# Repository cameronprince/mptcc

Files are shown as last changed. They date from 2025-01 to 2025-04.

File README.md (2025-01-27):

# MicroPython Tesla Coil Controller (MPTCC)

A MicroPython-based controller for Tesla coils, developed by Cameron Prince.

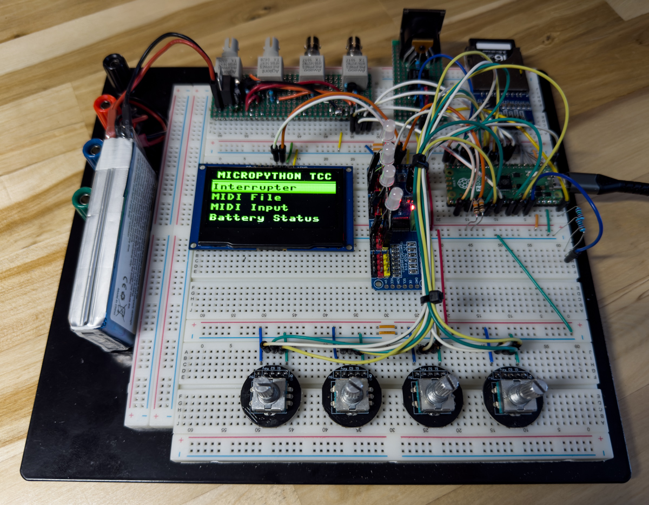
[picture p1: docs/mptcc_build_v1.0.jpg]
MicroPython Tesla coil controller build


This project is based on the MIDI Pro Tesla Coil Controller (also MPTCC) by Phillip Slawinski. A best
effort was made to maintain control functionality matching Phillip's controller, along with feature
parity with the initial Interrupter, MIDI File and MIDI Input screens. A few new features were added
as well, and more are planned.

The controller has four outputs which can drive fiber optic transmitters of your choice, or you may
use other connectors, such as BNC, with shielded cables. The controller sends pulsed square waves of
a frequency and duty cycle you control with the rotary encoders while on the Interrupter screen. On the MIDI
input screen, the controller takes the notes it receives from a MIDI instrument and converts them into
pulses matching the frequency and velocity of the received notes and sends them to all outputs.

The MIDI File screen lists MIDI files found on the SD card and allows you to map tracks within a selected
file with each of the four outputs. During playback, the four rotary encoders control the levels of
each output. The RGB LEDs are active any time the outputs are active and their colors match the relative
level of each output with colors ranging from green, to yellow, to red.

This software provides a framework for any number of screens with each screen optionally having any number
of sub-screens. The rotary encoder and pushbutton inputs cascade down to each screen or sub-screen,
ensuring that all code for a particular screen is contained within its class. Adding your own screens
to customize the controller should be pretty straightforward.

Please be aware that this is my first significant work with MicroPython. I am certain this software can
be improved in many ways and I invite anyone to participate.

## Table of Contents

- [Warning](#warning)
- [Features](#features)
- [Hardware](#hardware)
- [Dependencies](#dependencies)
- [Diagram](#diagram)
- [Connections](#connections)
- [Installation](#installation)
- [Usage](#usage)
- [File Descriptions](#file-descriptions)
- [License](#license)
- [Credits](#credits)

## Warning

Tesla coils are dangerous devices which can cause shocks, burns, fires and even death. The author assumes no
responsibility for any devices operated by the controller project described herein, or for any damage or
injury that may be caused by their operation.

This controller is experimental. If not assembled and operated correctly, it can cause damage to driver and
bridge components. It is solely up to the builder to verify the controller output prior to connecting it to
a Tesla coil. The author assumes no responsibility for damage to equipment, components, tools, etc. which can be
caused by the use of this controller. You have been warned.

## Features

- Class-based, modular screen management system
- Interrupt-driven inputs/non-polling design
- Utilizes threads for driving outputs
- Standard interrupter (square wave pulse generator) with variable frequency and on time and user configurable limits (currently drives all four outputs equally)
- MIDI file playback from SD card with elapsed time display and interface for mapping tracks to outputs - rotary encoders allow level control for each output
- Automatic scrolling of long file and track names
- MIDI input (currently drives all four outputs from a single input/channel)
- RGB LEDs display relative output levels as colors ranging from green, to yellow, to red
- Battery status monitoring
- User configuration stored in flash memory with restore defaults feature
- Intuitive menu system and navigation
- Easily expandable to support additional features
- Supports SSD1306, SSD1309, SSD1322 displays
- Supports standard quadrature rotary encoders and I2CEncoders w/ RGB LED
- Tested with both Raspberry Pi Pico 2 and ESP-WROOM-32

## Hardware
1. Raspberry Pi Pico 2 (Qty 1) [Buy](https://amzn.to/4hhQxz3) - or similar MicroPython-compatible microcontroller with at least two cores
2. PCA9685 16-channel 12-bit PWM (Qty 1) [Buy](https://amzn.to/4jf2E1J)
3. SD card reader (Qty 1) [Buy](https://amzn.to/40gHUhw)
4. Rotary encoder w/ switch (Qty 4) [Buy](https://www.amazon.com/dp/B0BGR4JPRK)
5. RGB LED (Qty 4) [Buy](https://amzn.to/3PD5WhP)
6. 2.4" SSD1309 OLED display (Qty 1) [Buy](https://amzn.to/40wQWbs) - or similar I2C-driven display with MicroPython frame buffer driver
7. 5-Pin DIN socket (Qty 1) [Buy](https://amzn.to/40hERpg)
8. 2N4401 NPN transistors (Qty 4) [Buy](https://amzn.to/4aikSeu)
9. 6N138 high-speed optocoupler (Qty 1) [Buy](https://amzn.to/3BXwgA4)
10. Fiber optic transmitters or connectors of your choice for outputs (Qty 4)
11. Various 1/4-watt resistors [Buy](https://amzn.to/3DXIOYx)
12. 1N4148 diode (Qty 1) [Buy](https://amzn.to/4hi579Q)
13. 5VDC power source (Qty 1) [Buy](https://amzn.to/3Wre4pd)
14. Optional breadboard (Qty 1) [Buy](https://amzn.to/4hkUC5s)

Total estimated cost: $160 USD (not including output transmitters or connectors)

## Dependencies
- Display driver ([MicroPython-SSD1306](https://github.com/TimHanewich/MicroPython-SSD1306))
- External PWM driver ([pca9685_for_pico](https://github.com/kevinmcaleer/pca9685_for_pico))
- Rotary encoder driver ([micropython-rotary](https://github.com/miketeachman/micropython-rotary))
- SD card reader driver ([sdcard.py](https://github.com/micropython/micropython-lib/blob/master/micropython/drivers/storage/sdcard/sdcard.py))
- MIDI input decoder ([SimpleMIDIDecoder](https://github.com/diyelectromusic/sdemp/blob/main/src/SDEMP/Micropython/SimpleMIDIDecoder.py))
- MIDI file parser ([umidiparser](https://github.com/bixb922/umidiparser))

## Schematic

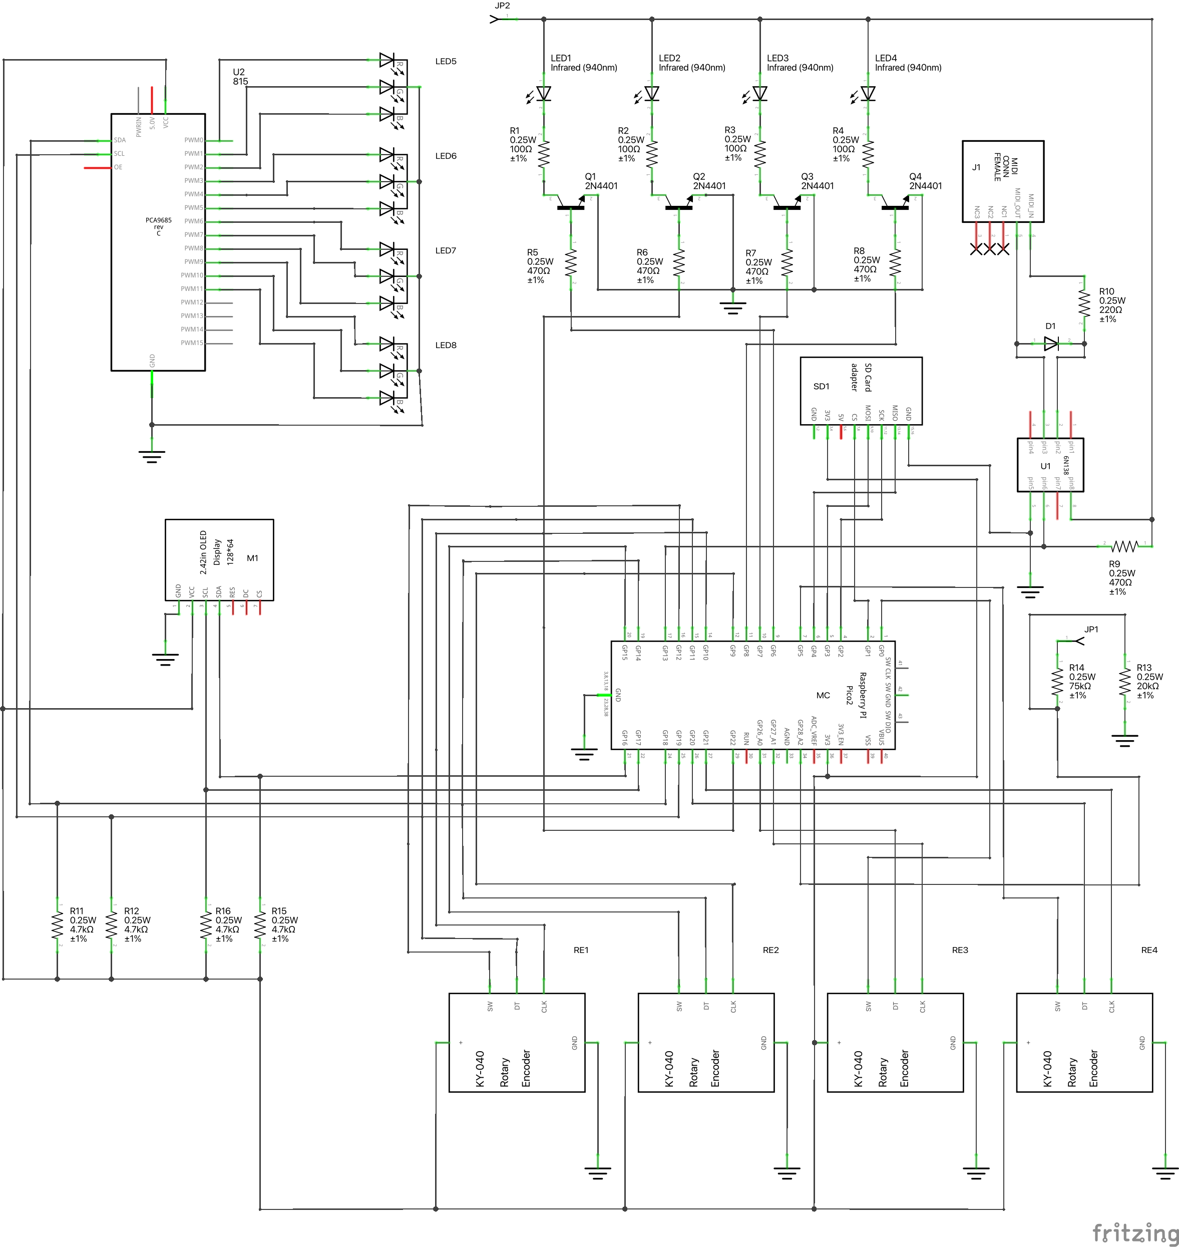
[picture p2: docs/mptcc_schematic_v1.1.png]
MicroPython Tesla coil controller schematic


## Diagram

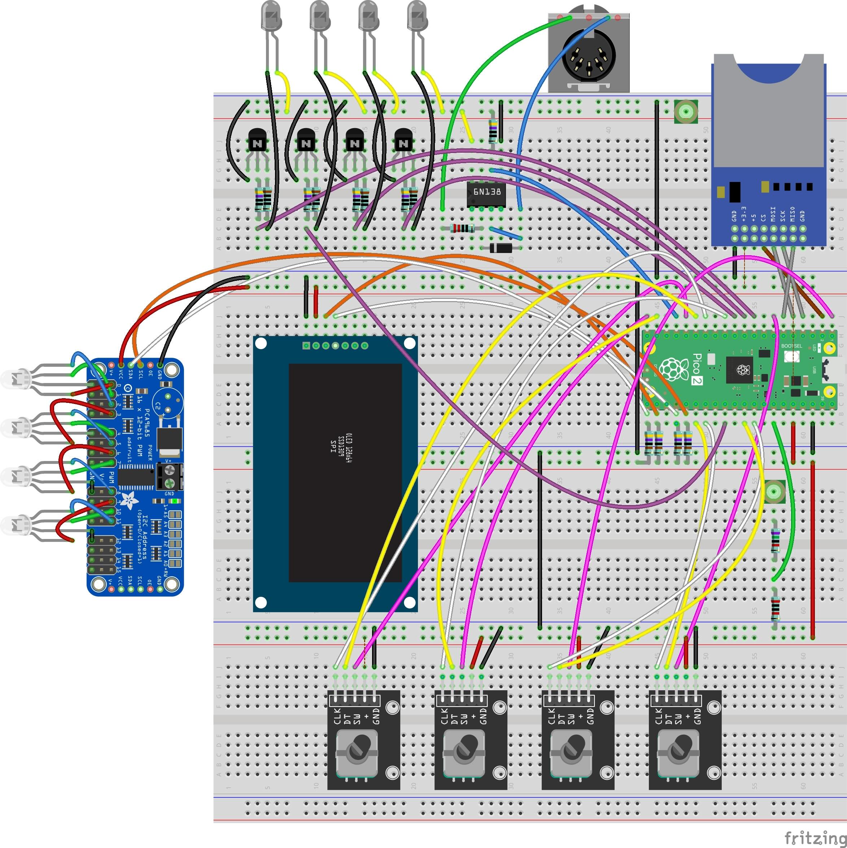
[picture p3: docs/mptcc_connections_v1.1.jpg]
MicroPython Tesla coil controller connections


You can download the Fritzing file for this project [here](docs/mptcc_v1.1.fzz).

## Installation

1. Clone the repository:

    ```bash
    git clone https://github.com/cameronprince/mptcc.git
    ```

2. Copy the project files to your MicroPython-compatible device. Typically, you place the entire mptcc directory into the root directory of your device.

3. Ensure you have the required dependencies installed on your device. The dependencies listed above should be placed into a lib subdirectory in the root directory of your device.

4. Edit the mptcc/init.py file and update any hardware variables for which your project deviates from the provided schematics and connection diagrams.

5. Run main.py

Custom firmware build instructions coming soon.

## Usage

### General Operation

Rotate encoder 1 to scroll through the main menu options. Press encoder 1 pushbutton to navigate to a sub-menu item
or select a screen. Pressing encoder 2 pushbutton is consistently used as the "back" or "return" button.

### Interrupter

On the interrupter screen, encoder 1 rotation sets output on time. Encoder 2 rotation sets
output frequency. Press encoder 3 pushbutton to enable/disable outputs. Pressing encoder 4
pushbutton triggers 10x mode where the frequency and on time increments by 10 rather than
the default of 1. To return to the main menu, press encoder 2 pushbutton.

### MIDI Input

When MIDI input is selected from the main menu, the controller immediately begins listening
for MIDI events on the MIDI port. This screen only has one input which is encoder 2 pushbutton
to stop listening for MIDI events and return to the main menu.

### MIDI File

The initial MIDI file screen shows a listing of MIDI files available on the SD card. Use encoder 1
rotation to scroll through the list of files. Press encoder 1 pushbutton to select a file. The
display will then show a list of MIDI tracks within the selected file. As with files, use encoder 1
to scroll through the list and press encoder 1 pushbutton to select a track. On the subsequent
assignment screen, rotate encoder 1 to cycle between None, 1, 2, 3 and 4. Pressing encoder 1 pushbutton
saves the assignment. Pressing encoder 2 pushbutton returns to the track listing without saving the assignment.

The number of track assignments for a selected MIDI file is displayed in the header of the track listing screen,
such as 2/4, indicating two of the maximum of four mappings have been made. Selecting an output for a track
which has already been assigned to a different track will result in the original assignment being overwritten.
Only a single track may be mapped to a single output.

Once track assignments are complete, press encoder 2 pushbutton to return to the file listing. You may then
press encoder 3 pushbutton to start playback. During playback, rotation of each encoder controls the level
of its corresponding output. Pressing any encoder pushbutton during playback will result in the player stopping.

### Battery Status

This screen is much like the MIDI input screen in that only encoder 2 pushbutton is active to allow returning
to the main menu. On this screen the current battery voltage is displayed. Depending on your setup and
battery voltage, you may need to adjust the drop factor in init.py and/or R13 and R14 values to obtain accurate values.

### Interrupter Configuration

This screen, and its two sub-screens, allow configuring upper and lower frequency and on time limits, as well
as a max duty cycle percentage. These values are immediately saved to flash memory when adjustments are made.
There is no "save" button in this case. Encoder 2 pushbutton should be used to exit the screen and encoder 3
and 4 pushbuttons cycle through the configuration sub-screens.

### Restore Defaults

This screen allows you to erase user configuration and return to a set of defaults. This configuration is
currently used only by the interrupter screen, but can be easily expanded to support additional screens
and configuration variables.

## File Descriptions

- `mptcc/main.py`: Main program file configured for Pico and default configuration.
- `mptcc/main_esp32.py`: Main program file configured for ESP-WROOM-32 and I2CEncoders.
- `mptcc/hardware/hardware.py`: Hardware parent class. (Placeholder for now)
- `mptcc/hardware/init.py`: Provides a method of sharing hardware configuration and objects between screens.
- `mptcc/hardware/output.py`: Provides the class for interfacing and controlling outputs.
- `mptcc/hardware/sd_card_reader.py`: Provides the class for interfacing with the SD card reader.
- `mptcc/hardware/display/display.py`: Display parent class. Provides display-related methods shared with child classes.
- `mptcc/hardware/display/ssd1306.py`: Display child class for interfacing with SSD1306 display library.
- `mptcc/hardware/display/ssd1309.py`: Display child class for interfacing with SSD1309 display library.
- `mptcc/hardware/display/ssd1322.py`: Display child class for interfacing with SSD1322 display library.
- `mptcc/hardware/input/input.py`: Input parent class. Provides input-related methods shared with child classes.
- `mptcc/hardware/input/i2cencoder.py`: Input child class for interfacing with I2CEncoder library.
- `mptcc/hardware/input/ky_040.py`: Input child class for interfacing with standard KY-040 rotary encoder.
- `mptcc/hardware/rgb_led/rgb_led.py`: RGB LED parent class. Provides shared methods for LED control.
- `mptcc/hardware/rgb_led/i2cencoder.py`: RGB LED child class for interfacing with I2CEncoder library.
- `mptcc/hardware/rgb_led/pca9685.py`: RGB LED child class for interfacing with RGB LEDS via PCA9685 external PWM board.
- `mptcc/lib/config.py`: Provides default user configuration values for the project.
- `mptcc/lib/menu.py`: Provides menu functionality.
- `mptcc/lib/utils.py`: Shared utility functions.
- `mptcc/screens/battery_status.py`: Displays the current battery status.
- `mptcc/screens/interrupter.py`: Provides the interrupter screen.
- `mptcc/screens/interrupter_config.py`: Provides the screen for configuring interrupter settings.
- `mptcc/screens/restore_defaults.py`: Provides the screen for restoring default settings.
- `mptcc/screens/__init__.py`: Imports each screen.
- `mptcc/screens/midi_input.py`: Provides the the MIDI input screen.
- `mptcc/screens/midi_file/midi_file.py`: Sets up sub-screen handlers for MIDI file playback.
- `mptcc/screens/midi_file/assignment.py`: Sub-screen for assigning tracks to outputs.
- `mptcc/screens/midi_file/files.py`: Sub-screen providing MIDI file listing from SD card.
- `mptcc/screens/midi_file/play.py`: Sub-screen providing MIDI file playback.
- `mptcc/screens/midi_file/tracks.py`: Sub-screen providing MIDI track listing.
- `mptcc/screens/midi_file/__init__.py`: Imports each MIDI file sub-screen.
- `mptcc/test_scripts/*`: Various hardware test scripts.

## License

This project is licensed under the MIT License. See the [LICENSE](LICENSE) file for more details.

## Credits

This project would not have been possible without Steve Ward and Phillip Slawinski. I've learned
a lot from these guys over the years and I appreciate the friendship I have with them.

Thanks to Hermann Paul von Borries (bixb922) for the umidiparser library and Kevin (diyelectromusic)
for the SimpleMIDIDecoder library.

Special thanks to Donna Whisnant, Tom Camp, Timur Tabi and Edwin Burwell for their encouragement,
guidance, support and code reviews.

---

Developed by Cameron Prince. Visit [teslauniverse.com](https://teslauniverse.com) for more information.

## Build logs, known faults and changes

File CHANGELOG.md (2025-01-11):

# Changelog

All notable changes to this project will be documented in this file.

## [Unreleased]

## [1.0.0] - 2025-01-06
### Added
- Initial release of the MicroPython Tesla Coil Controller (MPTCC).

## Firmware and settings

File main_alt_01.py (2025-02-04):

"""
MicroPython Tesla Coil Controller (MPTCC)
by Cameron Prince
teslauniverse.com

main.py
Defines and initializes the hardware and menu.
"""

# Prepare the init object to store configuration and initialized hardware.
from mptcc.hardware.init import init

"""
Hardware Settings
"""
# I2C bus 1 pin assignments and settings.
# (used by the I2CEncoders.)
init.PIN_I2C_1_SCL = 19
init.PIN_I2C_1_SDA = 18
init.I2C_1_INTERFACE = 1
init.I2C_1_FREQ = 400000

# I2CEncoder V2.1 settings.
init.I2CENCODER_ADDRESSES = [0x50, 0x30, 0x60, 0x48]
init.PIN_I2CENCODER_INTERRUPTS = [21, 22, 26, 27]

# SPI bus 1 pin assignments and settings.
# (used by the SD card reader)
init.SPI_1_INTERFACE = 0
init.SPI_1_BAUD = 1000000
init.PIN_SPI_1_SCK = 2
init.PIN_SPI_1_MOSI = 3
init.PIN_SPI_1_MISO = 4
init.PIN_SPI_1_CS = 1
# init.PIN_SPI_1_DC = 0
# init.PIN_SPI_1_RST = 0

# SPI bus 2 pin assignments and settings.
# (used by the display.)
init.SPI_2_INTERFACE = 1
init.SPI_2_BAUD = 16000000
init.PIN_SPI_2_SCK = 10
init.PIN_SPI_2_MOSI = 11
init.PIN_SPI_2_MISO = None
init.PIN_SPI_2_CS = 13
init.PIN_SPI_2_DC = 12
init.PIN_SPI_2_RST = 14

# Output pin assignments.
init.PIN_OUTPUT_1 = 9
init.PIN_OUTPUT_2 = 8
init.PIN_OUTPUT_3 = 7
init.PIN_OUTPUT_4 = 6

# Battery status ADC pin assignment and settings.
init.PIN_BATT_STATUS_ADC = 28
# Adjust for specific supply voltage used.
init.VOLTAGE_DROP_FACTOR = 848.5

# MIDI input pin assignment and UART settings.
init.PIN_MIDI_INPUT = 17
init.UART_INTERFACE = 0
init.UART_BAUD = 31250

# Miscellaneous definitions.
init.SD_MOUNT_POINT = "/sd"
init.CONFIG_PATH = "/mptcc/config.json"

# Frequencies listed here are filtered from the available choices for the interrupter function.
init.BANNED_INTERRUPTER_FREQUENCIES = []

# Rotary encoder pin assignments.
# init.PIN_ROTARY_1_CLK = 11
# init.PIN_ROTARY_1_DT = 10
# init.PIN_ROTARY_1_SW = 12

# init.PIN_ROTARY_2_CLK = 14
# init.PIN_ROTARY_2_DT = 9
# init.PIN_ROTARY_2_SW = 15

# init.PIN_ROTARY_3_CLK = 26
# init.PIN_ROTARY_3_DT = 27
# init.PIN_ROTARY_3_SW = 0

# init.PIN_ROTARY_4_CLK = 20
# init.PIN_ROTARY_4_DT = 21
# init.PIN_ROTARY_4_SW = 5

# Enable/disable encoder pin pull-up resistors.
# Most of the PCB-mounted encoders have pull-ups on the boards.
# init.ROTARY_PULL_UP = False

"""
Display

Select one of the display options below by commenting out the default option
and removing the comment for the desired, alternate option.

The display needs to be initialized first as it needs a large block of
contigious memory.

Edit the class for the selected hardware to define configuration.
"""
# SSD1306 0.96" 128X64 OLED LCD Display (https://amzn.to/40sf11I)
# Requires: https://github.com/TimHanewich/MicroPython-SSD1306
# Note: This library only supports standard frame buffer commands.
# from mptcc.hardware.display.ssd1306 import SSD1306 as display  # Default option.

# SSD1309 2.42" 128x64 OLED LCD Display (https://amzn.to/40wQWbs)
# Requires: https://github.com/rdagger/micropython-ssd1309
# Note: This library supports custom fonts, shapes, images, and more, beyond
# the standard frame buffer commands. This driver also works with SSD1306 displays.
# from mptcc.hardware.display.ssd1309 import SSD1309 as display  # Alternate option.

# SSD1322 3.12" 256x64 OLED LCD Display (https://amzn.to/4jupi6c)
# Requires: https://github.com/rdagger/micropython-ssd1322
# Note: This library supports custom fonts, shapes, images, and more, beyond
# the standard frame buffer commands. Note, this is an SPI device. You must pass
# an 'spi' argument when instantiating the display object as: init.display = display('spi').
from mptcc.hardware.display.ssd1322 import SSD1322 as display  # Alternate option.

init.display = display()

"""
Input Devices

Select one of the input device options below by commenting out the default option
and removing the comment for the desired, alternate option.

Edit the class for the selected hardware to define configuration.
"""
# KY-040 Rotary Encoder - https://amzn.to/42E63l1 or https://amzn.to/3CdzIqi
# Requires: https://github.com/miketeachman/micropython-rotary
# from mptcc.hardware.input.ky_040 import KY040 as inputs  # Default option.

# I2CEncoder V2.1 - https://github.com/Fattoresaimon/I2CEncoderV2.1
# Requires: https://github.com/cameronprince/i2cEncoderLibV2
from mptcc.hardware.input.i2cencoder import I2CEncoder as inputs  # Alternate option.

init.inputs = inputs()

"""
RGB LEDs

Select one of the RGB LED options below by commenting out the default option
and removing the comment for the desired, alternate option.

Edit the class for the selected hardware to define configuration.
"""
# PCA9685 16-channel 12-bit PWM - https://amzn.to/4jf2E1J
# Requires: https://github.com/kevinmcaleer/pca9685_for_pico
# from mptcc.hardware.rgb_led.pca9685 import PCA9685 as rgb_led  # Default option.

# I2CEncoder V2.1 - https://github.com/Fattoresaimon/I2CEncoderV2.1
# Requires: https://github.com/cameronprince/i2cEncoderLibV2
from mptcc.hardware.rgb_led.i2cencoder import I2CEncoder as rgb_led  # Alternate option.

init.rgb_driver = rgb_led()

"""
Outputs
"""
from mptcc.hardware.output import Output as output
init.output = output()

"""
SD Card Reader
"""
from mptcc.hardware.sd_card_reader import SDCardReader as sd_card_reader
init.sd_card_reader = sd_card_reader()

"""
Menu Definition
"""
from mptcc.lib.menu import Menu, MenuScreen, SubMenuItem, CustomItem
import mptcc.screens as screens

# Define and display the menu.
init.menu = Menu(
    init.display,
    init.display.DISPLAY_ITEMS_PER_PAGE,
    init.display.DISPLAY_LINE_HEIGHT,
    init.display.DISPLAY_FONT_WIDTH,
    init.display.DISPLAY_FONT_HEIGHT
)

init.menu.set_screen(MenuScreen('MicroPython TCC')
    .add(screens.Interrupter('Interrupter'))
    .add(screens.MIDIFile('MIDI File'))
    .add(screens.MIDIInput('MIDI Input'))
    .add(screens.BatteryStatus('Battery Status'))
    .add(SubMenuItem('Configure')
        .add(screens.InterrupterConfig('Interrupter'))
        .add(screens.MIDIFileConfig('MIDI File'))
        .add(screens.RestoreDefaults('Restore Defaults'))
    )
)

init.menu.draw()

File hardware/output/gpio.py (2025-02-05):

"""
MicroPython Tesla Coil Controller (MPTCC)
by Cameron Prince
teslauniverse.com

hardware/output/gpio.py
Class for driving outputs with GPIO PWM.
"""

from machine import Pin, PWM
from ...lib import utils
from ...hardware.init import init
from ..output.output import Output

class GPIO(Output):
    """
    A class to provide GPIO PWM outputs for the MPTCC.

    Attributes:
    -----------
    init : object
        The initialization object containing configuration and hardware settings.
    output : list
        A list of PWM objects for each output.
    """
    def __init__(self):
        super().__init__()
        self.init = init

        self.output = [
            PWM(Pin(self.init.PIN_OUTPUT_1)),
            PWM(Pin(self.init.PIN_OUTPUT_2)),
            PWM(Pin(self.init.PIN_OUTPUT_3)),
            PWM(Pin(self.init.PIN_OUTPUT_4))
        ]

    def disable_outputs(self):
        """
        Disables all outputs by setting their duty cycle to 0 and turning off the associated LEDs.
        """
        for output in self.output:
            output.duty_u16(0)
        for led in self.init.rgb_led:
            led.off()

    def set_output(self, output, active, frequency=None, on_time=None, triggering_class=None):
        """
        Sets the output based on the provided parameters.

        Parameters:
        ----------
        output : int
            The index of the output to be set.
        active : bool
            Whether the output should be active.
        frequency : int, optional
            The frequency of the output signal.
        on_time : int, optional
            The on time of the output signal in microseconds.
        triggering_class : object, optional
            The class instance containing max_duty, min_on_time, and max_on_time attributes.

        Raises:
        -------
        ValueError
            If frequency or on_time is not provided when activating the output.
        """
        if active:
            if frequency is None or on_time is None:
                raise ValueError("Frequency and on_time must be provided when activating the output.")
            
            frequency = int(frequency)
            on_time = int(on_time)

            self.output[output].freq(frequency)
            duty_cycle = int((on_time / (1000000 / frequency)) * 65535)
            self.output[output].duty_u16(duty_cycle)

            # The triggering class is passed for any screen which allows
            # variable signal constraints. The constraints are then used to
            # determine the output percentage level of the current signal.
            if triggering_class:
                percent = utils.calculate_percent(frequency, on_time, triggering_class)
                self.init.rgb_led[output].status_color(percent)
            else:
                # MIDI signal constraints are fixed at 0-127 by the standard.
                percent = utils.calculate_midi_percent(frequency, on_time)
                # print('CH: ', output, ' %:', percent)
                self.init.rgb_led[output].status_color(percent)
        else:
            self.output[output].duty_u16(0)
            self.init.rgb_led[output].off()

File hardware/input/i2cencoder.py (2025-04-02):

"""
MicroPython Tesla Coil Controller (MPTCC)
by Cameron Prince
teslauniverse.com

hardware/input/i2cencoder.py
Input and RGB LED module for I2CEncoder V2.1.
Also supports I2CEncoder Mini.
"""

import time
import uasyncio as asyncio
from machine import Pin
from ...lib.duppa import DuPPa
from ...hardware.init import init
from ..input.input import Input
from ...lib.utils import hex_to_rgb
from ..rgb_led.rgb_led import RGB, RGBLED

# Constants and register definitions for both types
CONSTANTS = {
    "mini": {
        "REG_GCONF": 0x00,
        "REG_INTCONF": 0x01,
        "REG_ESTATUS": 0x02,
        "REG_CVALB4": 0x03,
        "REG_CMAXB4": 0x07,
        "REG_CMINB4": 0x0B,
        "REG_ISTEPB4": 0x0F,
        "REG_DPPERIOD": 0x13,
        "WRAP_ENABLE": 0x01,
        "DIRE_LEFT": 0x02,
        "RMOD_X1": 0x00,
        "RESET": 0x80,
        "PUSHP": 0x02,
        "RINC": 0x10,
        "RDEC": 0x20,
    },
    "rgb": {
        "REG_GCONF": 0x00,
        "REG_INTCONF": 0x04,
        "REG_ESTATUS": 0x05,
        "REG_GCONF2": 0x30,
        "REG_PUSHP": 0x02,
        "REG_RINC": 0x08,
        "REG_RDEC": 0x10,
        "REG_CVALB4": 0x08,
        "REG_CMAXB4": 0x0C,
        "REG_CMINB4": 0x10,
        "REG_ISTEPB4": 0x14,
        "REG_ANTBOUNC": 0x1E,
        "REG_GAMRLED": 0x27,
        "REG_GAMGLED": 0x28,
        "REG_GAMBLED": 0x29,
        "REG_RLED": 0x18,
        "REG_GLED": 0x19,
        "REG_BLED": 0x1A,
        "CLK_STRECH_ENABLE": 0x0100,
        "RGB_ENCODER": 0x0020,
        "STD_ENCODER": 0x0000,
        "GAMMA_2": 3,
        "INT_DATA": 0x0000,
        "WRAP_ENABLE": 0x0002,
        "DIRE_RIGHT": 0x0000,
        "IPUP_ENABLE": 0x0000,
        "RMOD_X1": 0x0000,
        "RESET": 0x80,
    }
}

class I2CEncoder(Input):
    def __init__(self, i2c_instance=1, i2c_addrs=[], interrupt_pin=None, type="rgb", default_color="#326400", threshold_brightness=32, full_brightness=255):
        super().__init__()
        self.init = init
        self.i2c_addrs = i2c_addrs
        self.interrupt_pin = interrupt_pin
        self.type = type
        self.default_color = default_color
        self.threshold_brightness = threshold_brightness
        self.full_brightness = full_brightness
        self.instances = []
        self.init_complete = False
        self.active_interrupt = False

        if i2c_instance == 2:
            self.init.init_i2c_2()
            self.i2c = self.init.i2c_2
            self.mutex = self.init.i2c_2_mutex
        else:
            self.init.init_i2c_1()
            self.i2c = self.init.i2c_1
            self.mutex = self.init.i2c_1_mutex

        if self.interrupt_pin is not None:
            self.interrupt_pin = Pin(self.interrupt_pin, Pin.IN, Pin.PULL_UP)
            self.interrupt_pin.irq(trigger=Pin.IRQ_FALLING, handler=self.interrupt_handler)

        for addr in self.i2c_addrs:
            encoder = DuPPa(self.i2c, addr, CONSTANTS[self.type])
            self.instances.append(encoder)
            self.init_encoder(encoder)

        self.init_complete = True
        asyncio.create_task(self.process_interrupt())

        instance_key = len(self.init.input_instances["encoder"]["i2cencoder"])

        if self.type == "rgb":
            self.init.RGB_LED_ASYNCIO_POLLING = True
            if 'i2cencoder' not in self.init.rgb_led_instances:
                self.init.rgb_led_instances['i2cencoder'] = []
            rgb_encoder_instances = []
            for instance in self.instances:
                led_instance = RGB_I2CEncoder(instance, self.mutex, self.default_color, self.threshold_brightness, self.full_brightness)
                rgb_encoder_instances.append(led_instance)
            self.init.rgb_led_instances['i2cencoder'].append(rgb_encoder_instances)

        print(f"I2CEncoder {instance_key} (type: {self.type}) initialized on I2C_{i2c_instance}")
        for i, addr in enumerate(self.i2c_addrs):
            print(f"- Encoder {i + 1}: I2C address 0x{addr:02X}")
        if self.type == "rgb":
            print(f"- RGB LEDs initialized (default color: {self.default_color})")
            print(f"- Asyncio polling: {self.init.RGB_LED_ASYNCIO_POLLING}")

    def init_encoder(self, encoder):
        self.init.mutex_acquire(self.mutex, "i2cencoder:init_encoder")
        encoder.reset()
        time.sleep(0.1)

        if self.type == "mini":
            encconfig = (CONSTANTS[self.type]["WRAP_ENABLE"] | CONSTANTS[self.type]["DIRE_LEFT"] | CONSTANTS[self.type]["RMOD_X1"])
            encoder.begin(encconfig)
            reg = (CONSTANTS[self.type]["PUSHP"] | CONSTANTS[self.type]["RINC"] | CONSTANTS[self.type]["RDEC"])
            encoder.writeInterruptConfig(reg)
            encoder.writeCounter(0)
            encoder.writeMax(100)
            encoder.writeMin(0)
            encoder.writeStep(1)
            encoder.writeDoublePushPeriod(10)
        else:
            encoder_type = CONSTANTS[self.type]["RGB_ENCODER"] if self.type == "rgb" else CONSTANTS[self.type]["STD_ENCODER"]
            encconfig = (CONSTANTS[self.type]["INT_DATA"] | CONSTANTS[self.type]["WRAP_ENABLE"] |
                         CONSTANTS[self.type]["DIRE_RIGHT"] | CONSTANTS[self.type]["IPUP_ENABLE"] |
                         CONSTANTS[self.type]["RMOD_X1"] | encoder_type)
            encoder.begin(encconfig)
            reg = (CONSTANTS[self.type]["REG_PUSHP"] | CONSTANTS[self.type]["REG_RINC"] | CONSTANTS[self.type]["REG_RDEC"])
            encoder.writeEncoder8(CONSTANTS[self.type]["REG_INTCONF"], reg)
            encoder.writeCounter(0)
            encoder.writeMax(100)
            encoder.writeMin(0)
            encoder.writeStep(1)
            encoder.writeAntibouncingPeriod(10)
            current_gconf2 = encoder.readEncoder8(CONSTANTS[self.type]["REG_GCONF2"])
            new_gconf2 = current_gconf2 | (CONSTANTS[self.type]["CLK_STRECH_ENABLE"] >> 8)
            encoder.writeEncoder8(CONSTANTS[self.type]["REG_GCONF2"], new_gconf2)
            if self.type == "rgb":
                encoder.writeGammaRLED(CONSTANTS[self.type]["GAMMA_2"])
                encoder.writeGammaGLED(CONSTANTS[self.type]["GAMMA_2"])
                encoder.writeGammaBLED(CONSTANTS[self.type]["GAMMA_2"])
                r, g, b = hex_to_rgb(self.default_color)
                dimmed_r = r * self.threshold_brightness // 255
                dimmed_g = g * self.threshold_brightness // 255
                dimmed_b = b * self.threshold_brightness // 255
                encoder.writeRGBCode((dimmed_r << 16) | (dimmed_g << 8) | dimmed_b)

        self.init.mutex_release(self.mutex, "i2cencoder:init_encoder")

    def interrupt_handler(self, pin):
        if not self.init_complete:
            return
        self.active_interrupt = True
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

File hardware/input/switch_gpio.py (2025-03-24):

"""
MicroPython Tesla Coil Controller (MPTCC)
by Cameron Prince
teslauniverse.com

hardware/input/switch_gpio.py
GPIO switch input driver.
"""

import time
from machine import Pin
from ...hardware.init import init
from ..input.input import Input
from ...lib.menu import Screen


class Switch_GPIO(Input):
    def __init__(self, pins, pull_up=True):
        """
        Initialize the GPIO switch driver.

        Args:
            pins (list): A list of GPIO pin numbers to use as switches.
            pull_up (bool): Whether to enable pull-up resistors for the switch pins.
        """
        super().__init__()

        self.pins = pins
        self.pull_up = pull_up
        self.last_switch_click_time = [0] * len(pins)  # Track last click time for debouncing.
        self.debounce_delay = 300  # Debounce delay in milliseconds.
        self.instances = []

        # Disable integrated switches in encoders.
        init.integrated_switches = False

        # Initialize GPIO pins for switches.
        self.switch_pins = []
        for i, pin in enumerate(self.pins):
            switch_pin = Pin(pin, Pin.IN, Pin.PULL_UP if self.pull_up else Pin.PULL_DOWN)
            switch_pin.irq(handler=lambda p, idx=i: self._handle_interrupt(idx), trigger=Pin.IRQ_FALLING)
            self.instances.append(switch_pin)

        # Print initialization details.
        print(f"GPIO switch driver initialized with {len(self.pins)} switches (pull_up={self.pull_up}):")
        for i, pin in enumerate(self.pins):
            print(f"- Switch {i + 1}: GPIO={pin}")

    def _handle_interrupt(self, idx):
        """
        Handle switch interrupts.

        Args:
            idx (int): The index of the switch.
        """
        current_time = time.ticks_ms()
        if time.ticks_diff(current_time, self.last_switch_click_time[idx]) > self.debounce_delay:
            self.last_switch_click_time[idx] = current_time
            self._handle_switch_click(idx + 1)  # Switch indices are 1-based.

    def _handle_switch_click(self, switch):
        """
        Handle a switch click event.

        Args:
            switch (int): The index of the switch (1-based).
        """
        print(switch)
        if switch <= 4:
            # Switches 1-4: Call the parent class's switch_click method.
            super().switch_click(switch)
        else:
            # Switches 5-6: Simulate encoder 1 rotation.
            # Ignore navigation switches when not displaying the menu.
            current_screen = self.init.menu.get_current_screen()
            if not isinstance(current_screen, Screen):
                direction = 1 if switch == 6 else -1  # Switch 5 = Previous, Switch 6 = Next.
                super().encoder_change(0, direction)  # Encoder 1 is index 0.

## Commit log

2025-01-13 Resetting repo to submit initial commit as a PR.
    [battery_status.py, init.py, interrupter.py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]
2025-01-16 Addresses reviewer feedback, final clean up and fixes.
    [battery_status.py, init.py, interrupter.py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]
2025-01-17 Adds variable for encoder pull up resistors and readme fix.
    [init.py]
2025-01-18 Adds diagram, schematic, fritzing and build image, updates readme.
    [mptcc_v1.0.fzz]
2025-01-18 Fixes missing routes on diagram and missing username in github link.
    [mptcc_v1.0.fzz]
2025-01-20 Begin refactoring hardware handling to support mulitple display and input types.
    [mptcc_v1.0.fzz]
2025-01-21 More hardware work - moves display to dedicated I2C & interrupter fix.
    [init.py, interrupter.py, ky_040.py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]
2025-01-22 Complates hardware refactor, bug fixes and moves PWM to dedicated I2C.
    [mptcc_v1.0.fzz, mptcc_v1.1.fzz]
2025-01-25 Begins refactor of inputs & adds esp32 example.
2025-01-27 Completes input refactor & completes support for I2CEncoder.
2025-01-27 Final updates and fixes.
    [ky_040.py, main_esp32.py]
2025-01-27 Interrupter fixes.
2025-01-30 Bug fixes & enhancements for 1.2.
    [i2cencoder.py, i2cencoder_encoder_test.py, i2cencoder_encoder_test_single.py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]
2025-01-30 Update PCA9685 RGB LED code to support refactor.
2025-02-01 Major MIDI file bug fix and more.
    [interrupter.py, main_alt_01.py, output.py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]
2025-02-03 Resolves track mapping issue & adds saved levels support.
    [main_alt_01.py]
2025-02-04 Bug fixes, consolidated rotary value handling.
    [i2cencoder.py, input.py, interrupter.py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]
2025-02-05 Sets up sub-classing for output & provides PIO driver.
2025-02-06 Bug fixes for PIO output subclass.
    [gpio_pio.py, gpio_pwm.py, main_alt_01.py]
2025-02-09 Adds support for MIDI tracks with no track name, fixes index issue.
    [i2cencoder.py, pca9685.py, rgb_led.py]
2025-02-09 Fixes track index issue.
2025-02-10 Switches scrolling to asyncio.
2025-02-11 Resolves track index issue.
2025-02-11 Normalizes interrupter config variables.
2025-02-13 More ARSG updates & interrupter/output refactoring.
2025-02-13 More ARSG work, refactoring, adds events, i2cencoder fixes.
    [arsg.py, gpio_pio.py, gpio_pwm.py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]
2025-02-14 Completes output, input, i2cencoder refactor & ARSG screen.
2025-02-15 Adds PCA9685 output driver.
2025-02-18 Checks in some fixes and recent work for 1.2.6.
    [gpio_pio.py, i2cencoder.py, pca9685.py]
2025-02-19 Adds support for I2CEncoderMini input devices.
2025-02-19 Adds mutex to PCA9685 LED driver, updates test scripts.
2025-02-20 Adds REG LED Ring Small RGB driver.
2025-02-21 Adds MPC23017 output drivers and bug fixes.
    [gpio_bitbang.py, i2cencoder.py, main_alt_01.py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]
2025-02-21 Renames PCA9685 output driver.
2025-02-27 More fixes and tweaks.
    [gpio_pwm.py, i2cencoder.py, init.py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]
2025-02-27 Another round of tweaks/fixes, stubs our Wombat 18AB output driver.
    [init.py, ky_040.py, ssd1306.py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]
2025-03-02 Updates to SSD1322 & RGB LED ring small drivers, tweaks & bugfixes.
    [rgb_led.py, rgb_led_ring_small.py, ssd1322.py]
2025-03-02 Restores comments/docs to SSD1322 driver.
2025-03-02 Fixes long-standing interrupt issue with i2cencoders.
    [i2cencoder.py]
2025-03-05 KY-040 driver updates.
2025-03-05 Adds default color and mutex fix to i2cencoder.
    [i2cencoder.py, i2cencoder_rgb_test.py, rgb_led_ring_small.py]
2025-03-05 Moves i2cencodermini and rgbledringsmall to new duppa library.
2025-03-06 Adds support for generic switch.
2025-03-12 Adds NeoPixel RGB LED driver & fixes a bug in PCA9685 output driver.
    [neopixel.py, pca9685.py]
